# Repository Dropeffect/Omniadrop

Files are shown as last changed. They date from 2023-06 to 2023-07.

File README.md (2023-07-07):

# Dropeffect GitHub
Welcome to the Dropeffect GitHub repository. This is a place to share the instructions, models, adapters and any other relevant files for the Dropeffect products from Dropeffect R&D team and other users. 

Check the folders under the product name to find the file you need. We will continue updating the folders.

# How to buy Dropeffect products
Check the reseller list from Dropeffect website: www.dropeffect.com/pages/resellers

# Note
Thank you for using Dropeffect products. If you have any questions during use, please do not hesitate to contact us: contact@dropeffect.com. We will work with you to solve it. 

For more product information you can always follow Dropeffect Website/Twitter/Instagram/Facebook/Youtube and GitHub. Thank you!

Dropeffect Website: www.dropeffect.com

Dropeffect Twitter: www.twitter.com/dropeffect

Dropeffect Instagram: www.instagram.com/drop_effect

Dropeffect Facebook: www.facebook.com/Dropeffect

Dropeffect Youtube: www.youtube.com/@DropEffect

# Youtube link
Detailed introduction video: www.youtube.com/watch?v=j66pk6BJIjA

# Disclaimers
All models are shared for personal use only and commercial use is prohibited.

Models reuploaded base on original author's statement.

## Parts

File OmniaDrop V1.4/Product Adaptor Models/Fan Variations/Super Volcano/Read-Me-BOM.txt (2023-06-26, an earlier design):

You need the following additional materials:

1x 4010 Blower Fan
2x ISO4762 M2x4mm for the top holes of the 4010 blower fans
2x ISO4762 M2x6mm for the bottom holes of the 4010 blower fans
2x ISO7380 M3x8mm to attach the "Cooling-Two-Fan" to the "Cooling-Block-Fan"
4x M3 threaded inserts, these are there to attach a probe holder. The top two threaded insert are intended for a BLTouch probe holder and the the bottom two threaded inserts are intended for a induction probe holder.

For reference there are two pictures how to assemble everything.

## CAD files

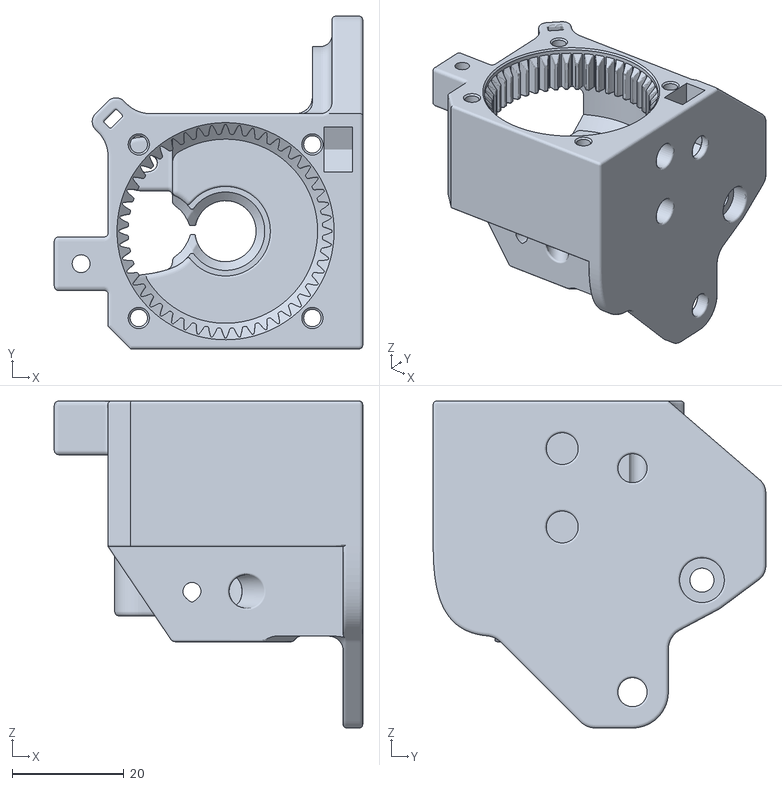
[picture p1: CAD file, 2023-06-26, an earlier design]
OmniaDrop V1.4/Product Adaptor Models/Ender 3/OmniaDrop-Elia-Ender3-Main 300 V1.4.stl
55.1 x 59.4 x 58.4

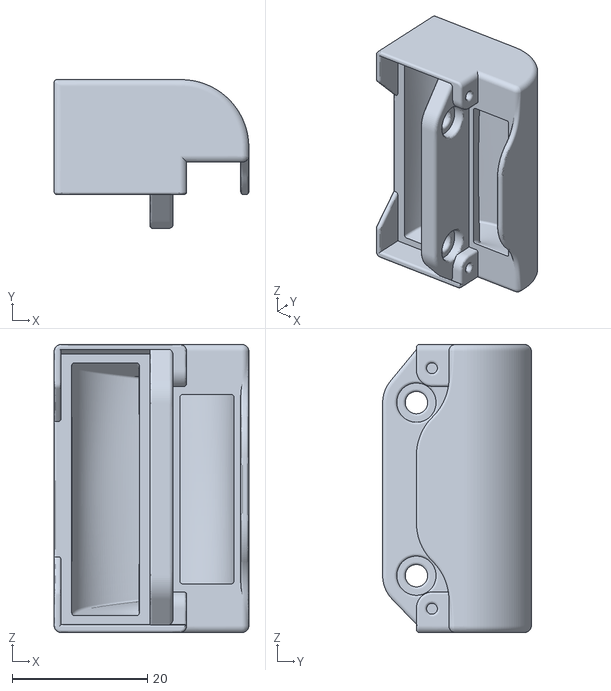
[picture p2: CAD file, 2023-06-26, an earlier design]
OmniaDrop V1.4/Product Adaptor Models/Fan Variations/Super Volcano/Cooling-Block-Fan-Super-Volcano.stl
28.8 x 22.0 x 42.6

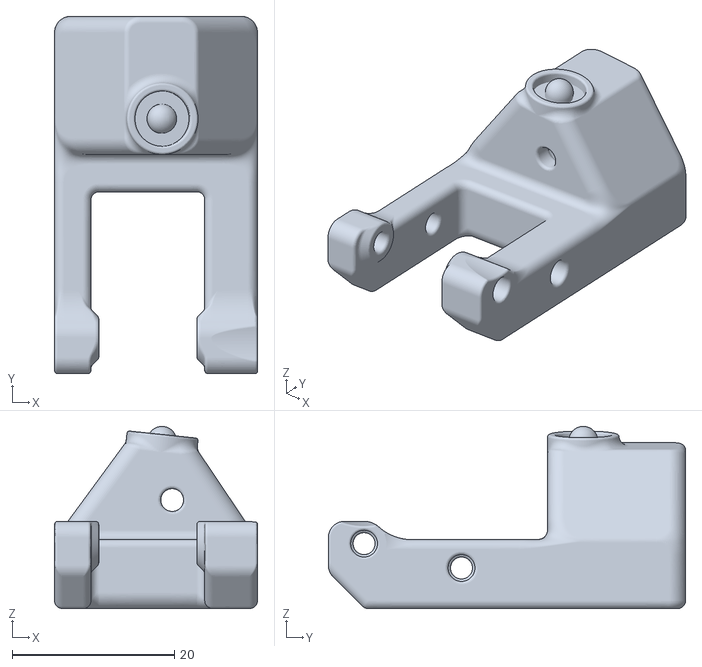
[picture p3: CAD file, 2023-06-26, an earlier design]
OmniaDrop V1.4/Product Adaptor Models/Idler Variations/OmniaDrop-175-Idler-Push-Fit.stl
25.0 x 44.0 x 22.4

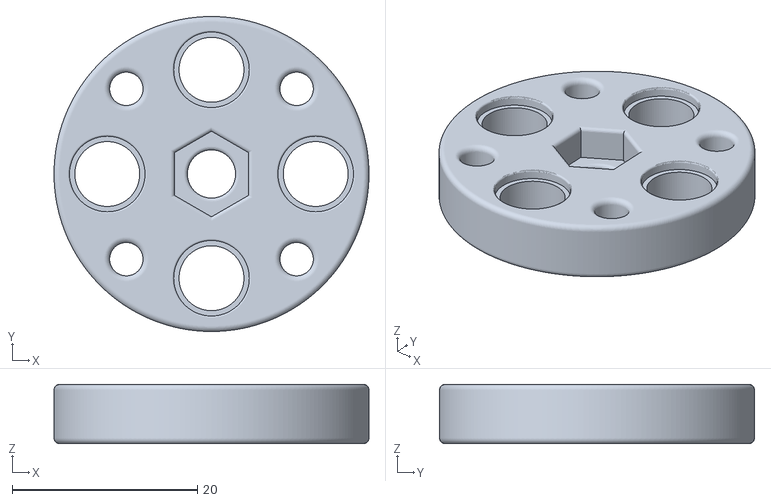
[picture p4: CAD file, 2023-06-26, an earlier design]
OmniaDrop V1.4/Product Adaptor Models/Planet-Disk V1.4.stl
34.0 x 34.0 x 6.40

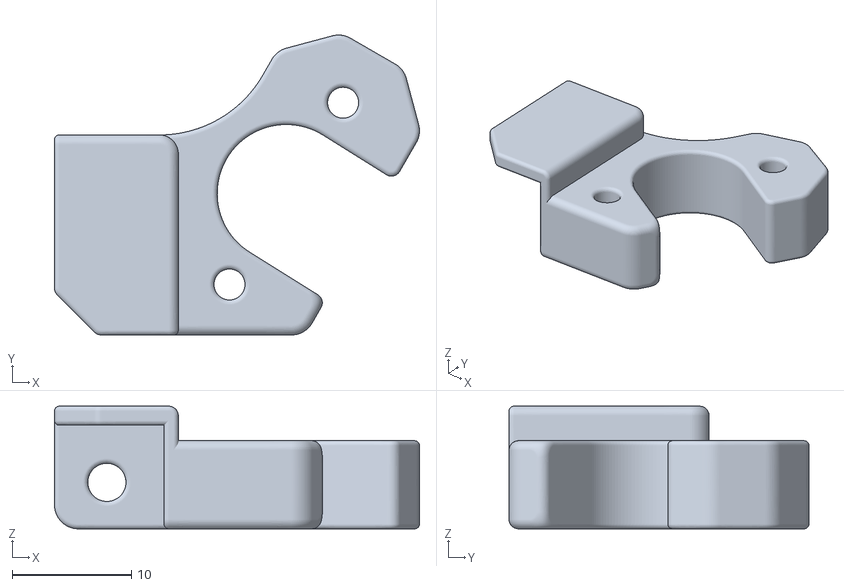
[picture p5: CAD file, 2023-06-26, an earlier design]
OmniaDrop V1.4/Product Adaptor Models/Probe Mounts/OmniaDrop-BLTouch-Clone.stl
30.7 x 25.2 x 10.3

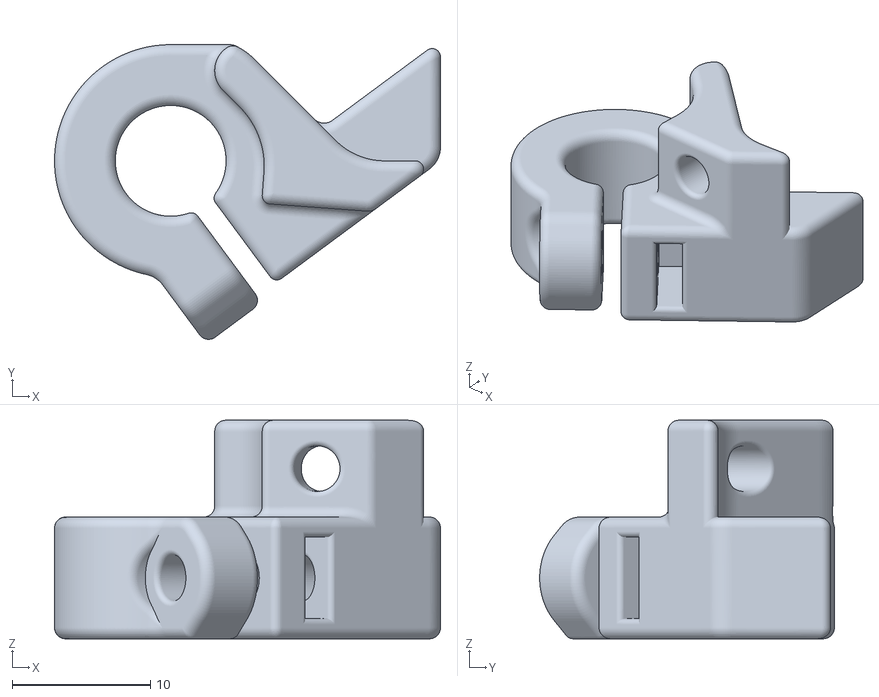
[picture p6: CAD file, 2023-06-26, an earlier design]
OmniaDrop V1.4/Product Adaptor Models/Prusa/OmniaDrop-Prusa-Probe 175 V1.4.stl
27.9 x 21.3 x 15.8

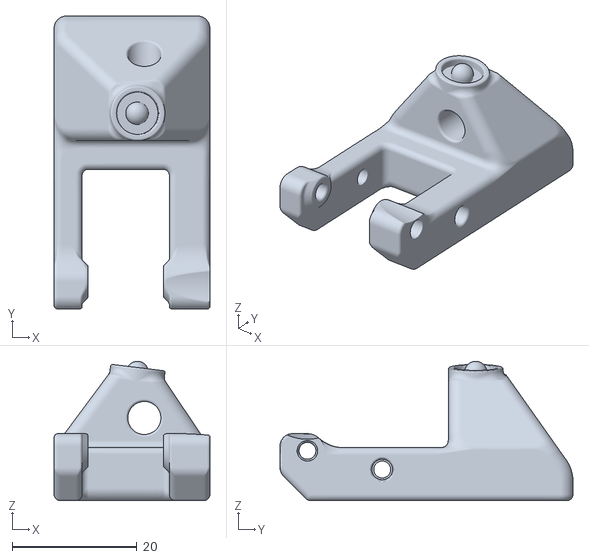
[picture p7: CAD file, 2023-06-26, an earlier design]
OmniaDrop V1.4/Product Adaptor Models/Standard/OmniaDrop-Idler 300 V1.4.stl
25.0 x 47.0 x 22.4

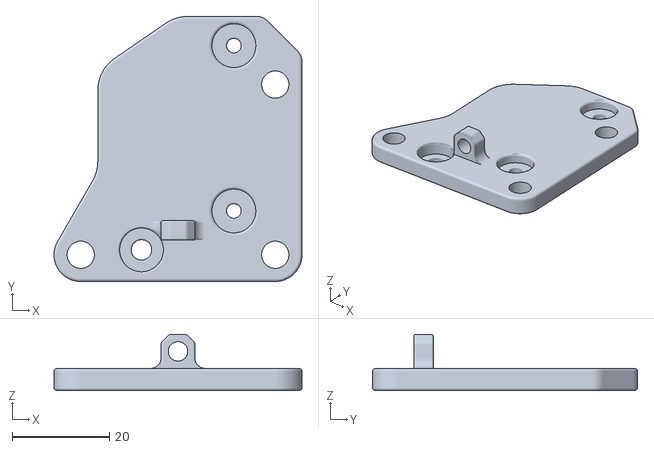
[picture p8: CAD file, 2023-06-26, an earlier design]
OmniaDrop V2.1/Product Adaptor Models/Artist-D Pro/OmniaDrop-Artist-D-Pro-Plate-right V2.1.stl
51.0 x 54.5 x 11.6

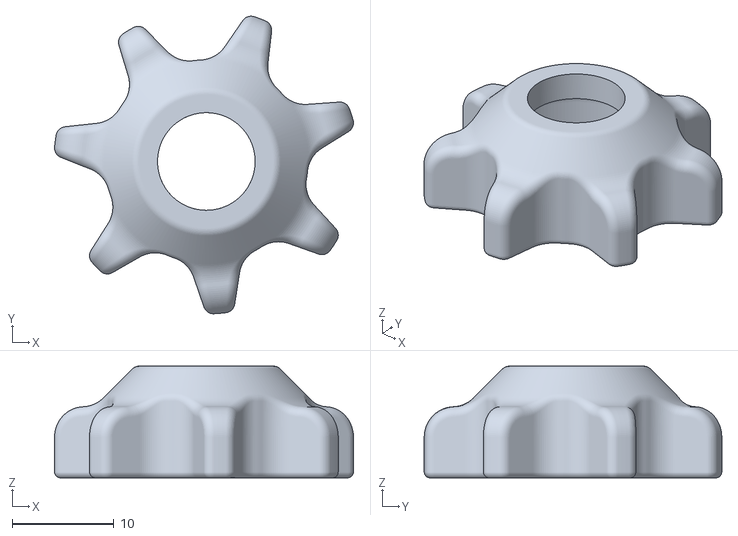
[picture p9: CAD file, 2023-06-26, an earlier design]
OmniaDrop V2.1/Product Adaptor Models/OmniaDrop-Manual-Wheel V2.stl
29.4 x 29.3 x 11.0

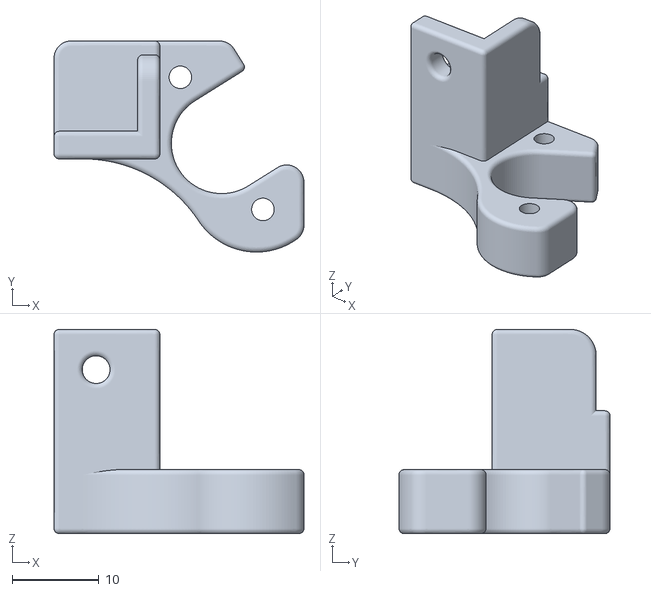
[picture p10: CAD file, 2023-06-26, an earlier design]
OmniaDrop V2.1/Product Adaptor Models/Probe Mounts/BLTouch-Clone-Mount.stl
28.9 x 24.4 x 23.6

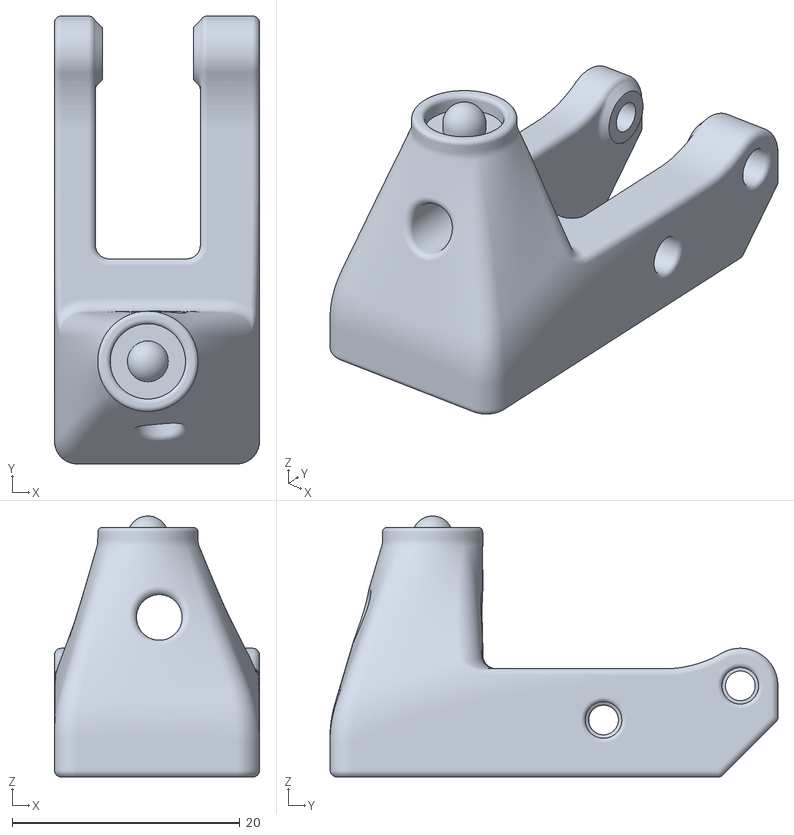
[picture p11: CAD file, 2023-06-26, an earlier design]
OmniaDrop V2.1/Product Adaptor Models/Prusa/OmniaDrop-Prusa-Idler V2.1.stl
18.0 x 39.3 x 22.9

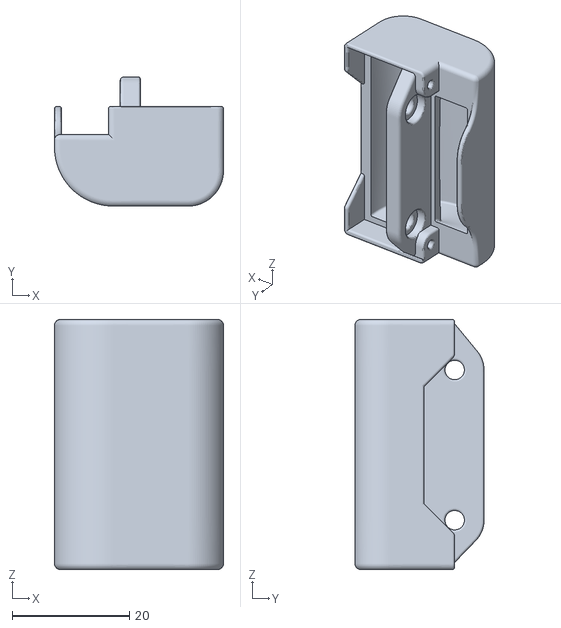
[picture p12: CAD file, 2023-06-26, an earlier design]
OmniaDrop V1.4/Product Adaptor Models/Only-Cooling-Block-Fan.stl
28.8 x 22.0 x 42.6

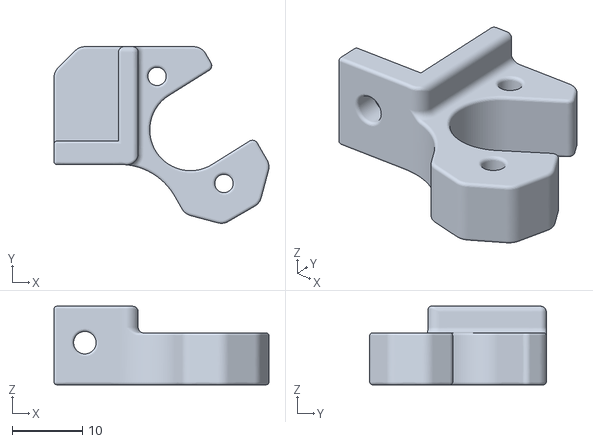
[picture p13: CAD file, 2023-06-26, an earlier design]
OmniaDrop V1.4/Product Adaptor Models/Probe Mounts/OmniaDrop-BLTouch-Standard.stl
30.7 x 25.2 x 11.2

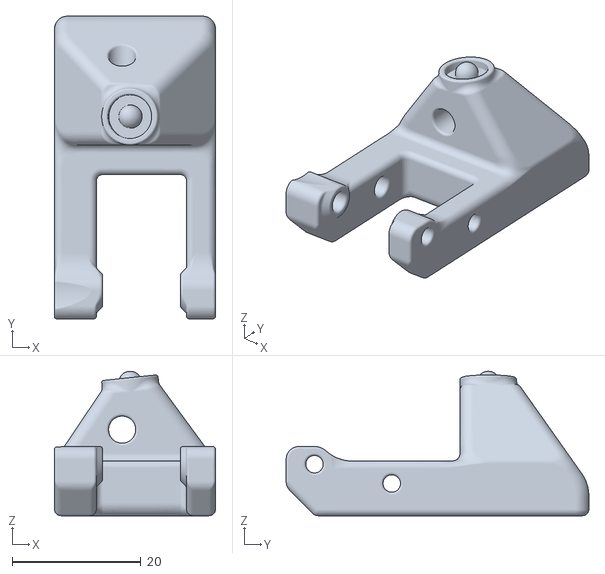
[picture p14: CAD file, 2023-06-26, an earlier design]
OmniaDrop V1.4/Product Adaptor Models/Prusa/OmniaDrop-Prusa-Idler 175 V1.4.stl
25.0 x 47.0 x 22.4

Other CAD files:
OmniaDrop V2.1/Product Adaptor Models/Standard/OmniaDrop-Idler-175 V2.1.stl
OmniaDrop V1.4/Product Adaptor Models/Standard/OmniaDrop-Manual-Wheel-ThreadedInsert.stl
OmniaDrop V2.1/Product Adaptor Models/Artist-D Pro/OmniaDrop-Artist-D-Pro-Plate-left V2.1.stl
OmniaDrop V2.1/Product Adaptor Models/Probe Mounts/BLTouch-Mount.stl
OmniaDrop V1.4/Product Adaptor Models/Probe Mounts/OmniaDrop-BLTouch-Volcano.stl
OmniaDrop V1.4/Product Adaptor Models/Probe Mounts/OmniaDrop-EZABL-18mm.stl
OmniaDrop V1.4/Product Adaptor Models/Standard/OmniaDrop-Idler 175 V1.4.stl
OmniaDrop V2.1/Product Adaptor Models/Prusa/OmniaDrop-Prusa-Cable V1.4.stl
OmniaDrop V2.1/Product Adaptor Models/Prusa/OmniaDrop-Prusa-Probe V2.1.stl

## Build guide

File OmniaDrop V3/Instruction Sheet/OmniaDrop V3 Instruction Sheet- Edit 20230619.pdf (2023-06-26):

## OmniaDrop Instructions and Assembly

## Dear customer, first of all thank you for purchasing the

## OmniaDrop V3 from DropEffect. When you open the

accessory package, you will find the following components.

No. | Name | Quantity
1 | H2.5 Hex Key | 1
2 | H2.0 Hex Key | 1
3 | H1.5 Hex Key | 1
4 | M5 Washer | 1
5 | Thermal Grease（0.5g） | 1
6 | M3 threaded inserts | 2
7 | M2 threaded inserts | 4
8 | H8.0 Open Spanner | 1
9 | Fan Extension Cable-5cm / JST-XHP | 2
10 | Motor Extension Cable-5cm / JST-XHP | 1
11 | Thermistor Extension Cable-5cm / JST-XHP | 1
12 | Heater Extension Cable-5cm | 1
13 | Fan Extension Cable-5cm / DuPont | 2
14 | Motor Extension Cable-5cm / DuPont | 1
15 | Thermistor Extension Cable-5cm / DuPont | 1

## Printing parameters

The nozzle size for printing the OmniaDrop parts should be a 0.4 mm nozzle or smaller. You should use 3 or more perimeters and 25% infill or more.

This part is important there should be no Z-Seam inside the blue sections of the OmniaDrop Extruder Main Body. The problem with a Z-Seam in these areas is that two ball bearings will be inserted into these grooves and if there is a Z-Seam in these areas then the planetary gears system will be off-centered and as such will not run smoothly. In your slicer it should be possible to edit your settings to position your Z-Seam accordingly.

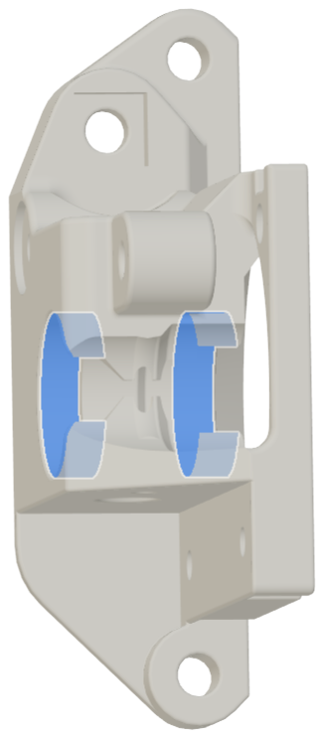
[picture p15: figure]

## Preparing the 3D printed parts

Components | QTY
Cooling fan duct | 1
Manual Wheel | 1
Extruder Main Body | 1
M2 threaded inserts | 4
M3 threaded inserts | 2
M6 threaded insert | 1

Use a soldering iron to insert the threaded inserts into the 3D printed parts. Ensure that the threaded inserts are flush and perpendicular. Be careful when using a soldering iron, they are very hot and you can burn yourself severely.

To get the M6 threaded insert of the manual wheel perpendicular you can use the Idler Dual Drive Gear (the shorter of the two Dual Drive Gear) as a base. Put the Idler Dual Drive Gear onto a non-flammable surface and put the manual wheel on top of it. This will ensure that the M6 threaded insert is inserted perpendicular and not too deep.

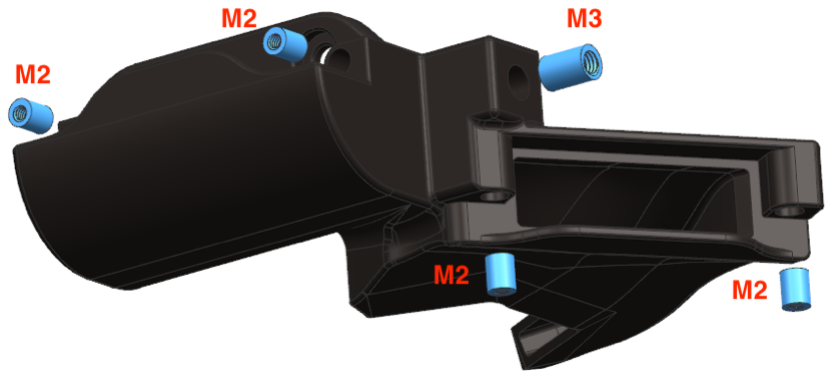
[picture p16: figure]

## Step 1

Components | QTY
M3x10 Hexagon button head screw | 4
Planetary gears | 4
Flanged ball bearings (F683 ZZ) | 8
Drive shaft (Planet Disk) | 1

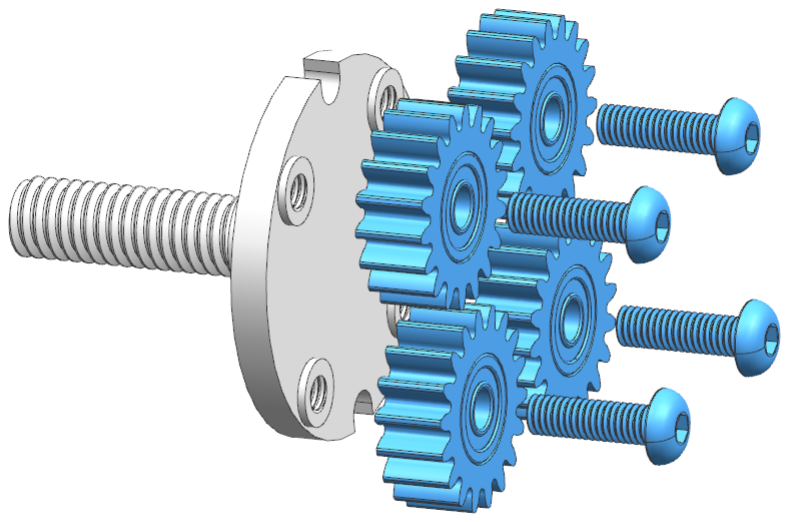
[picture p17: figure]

Insert two F683 ZZ ball bearings into a planet gear. Now use a M3×10 screw to attach the planet gear onto the Planet Disk. Please ensure that the planet gear is orientated in such a way that the protruding ball bearing of the planet gear interfaces with the Planet Disk. Repeat this for the remaining three planet gears.

## Step 2

Components | QTY
M6 threaded Drive Gear | 1
16 mm Ball Bearing (688ZZ W4) | 1
Extruder Main Body | 1

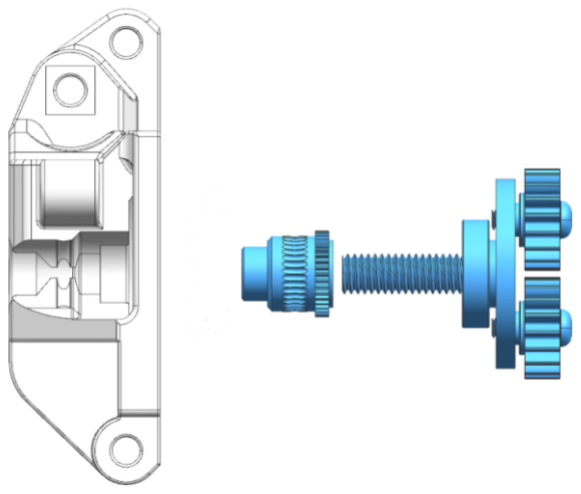
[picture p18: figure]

Put a 688ZZ W4 ball bearing (16 mm Diameter) onto the drive shaft of the Planet Disk. Tighten the M6 threaded drive gear onto the drive shaft. Finally insert the assembled drive shaft into the center hole of the extruder main body.

## Step 3

Components | QTY
M3 washer | 1
M3x8 Hexagon button head screw | 1
16 mm Ball Bearing (688ZZ W4) | 1
Manual Wheel | 1

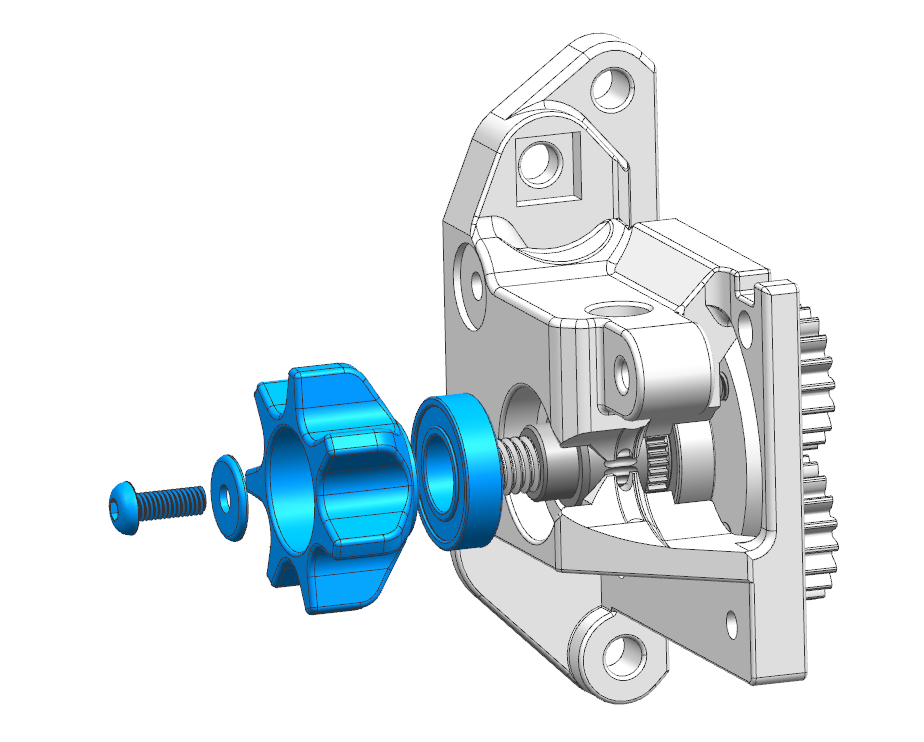
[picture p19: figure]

Press the 688ZZ W4 drive gear bearing into the front groove of the extruder main body. Then thread the manual wheel on the drive shaft to tighten everything down. Secure the position of the manual wheel by using a M3 washer and a M3x8 screw.

## Step 4

Components | QTY
M4x16 Hexagon button head screw | 1
Knurled nut | 1
M4 Square nut | 1
Spring | 1
Collect | 1
Collect clip | 1

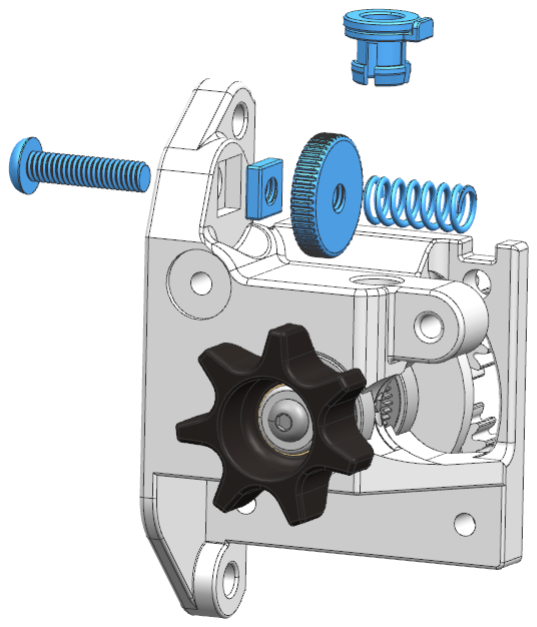
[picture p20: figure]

Insert the collect into the extruder main body and fix it with the collect clip. Insert the M4 square nut into the rectangular groove of the extruder main body and use the M4x16 screw to tighten everything down. Screw the knurled nut onto the M4 screw and place the compression spring onto the screw.

## Step 5

Components | QTY
M3x16 Hexagon button head screw | 2
Idler gear | 1
7mm ball bearing (683ZZ) | 2
Idler gear arm | 1

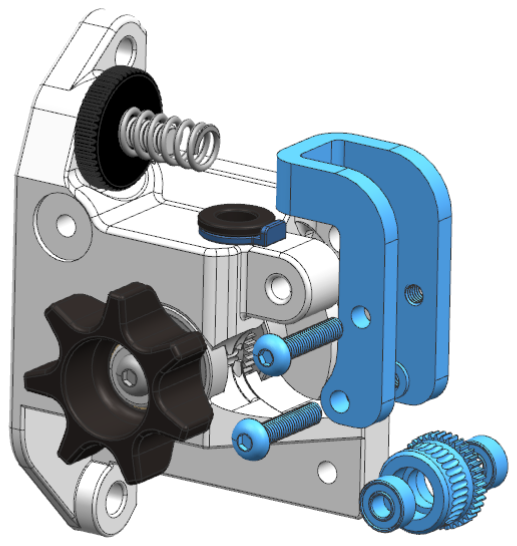
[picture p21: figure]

Insert two 683ZZ ball bearings into the internal holes of the idler gear. Place the Idler gear with the two ball bearings at bottom hole of the idler gear arm. Use a M3x16 screw to fix the position of the Idler gear; do not tighten it down too much, ensure that the Idler gear can spin freely. Use the second M3x16 screw to attach the Idler arm to the extruder main body. Again, do not tighten down the screw too much. The intention of these two M3x16 screws is not to tighten anything down, they should just hold the Idler gear and arm in position.

## Step 6

Components | QTY
M3x10 Hexagon button head screw | 1
M3x35 Hexagon button head screw | 1
M3 washer | 1
Ring Gear | 1
Nema 17 | 1

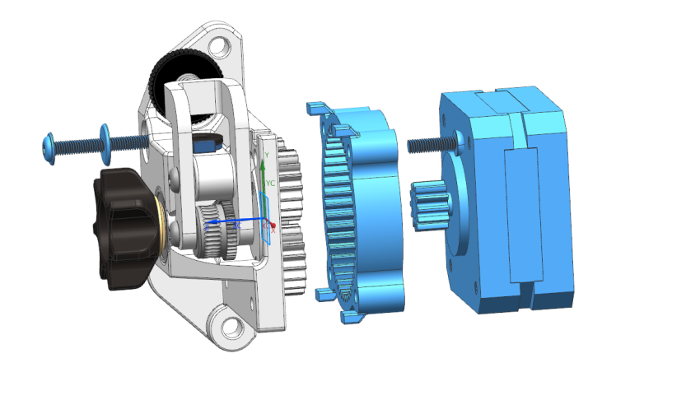
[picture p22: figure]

Attach the ring gear on the extruder main body. The four pegs on the ring gear should glide into the extruder main body. There are two indentations on the four 3 mm through holes of the ring gear, these should be orientated so that they are at the top section of the extruder main body. Use a M3×10 screw to secure the ring gear on the extruder main body. Now install the Nema 17 stepper motor on the planetary gear system and secure it using a M3x35 screw with a M3 washer.

## Step 7

Components | QTY
Heatbreak | 1
Thermal grease | 1
M3x35 Hexagon button head screw | 2
Heatsink | 1
Ring Heater | 1
Nozzle | 1

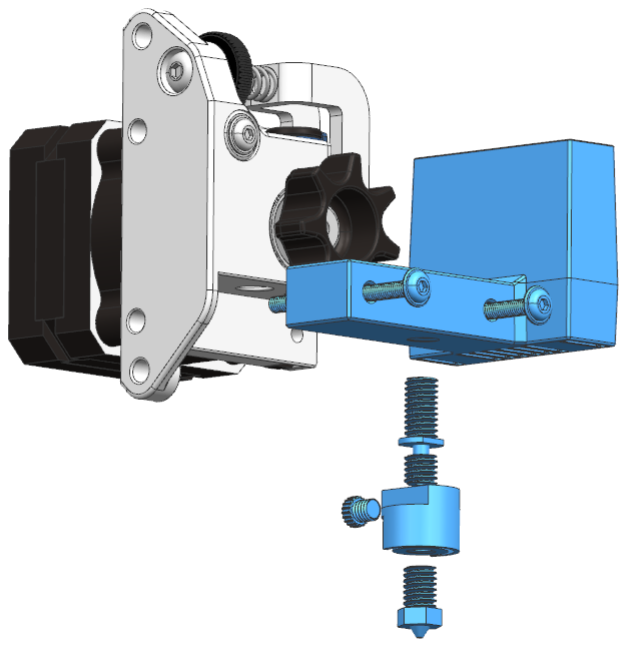
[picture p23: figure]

Apply some thermal grease onto the long threads of the heat break and screw it into the heat sink. Do NOT apply thermal grease onto the short threads of the heatbreak. Screw the Ring Heater with the indentations facing towards the heatsink onto the short thread of the heatbreak until no more threads are visible. However, do NOT screw the Ring Heater until it touches the heatsink, the “bottle neck” section of the heatbreak should always be visible. Orientate the cables of the Ring Heater so that they are facing the stepper motor. Finally, screw the nozzle into the Ring Heater and tighten it down. Please ensure that you do NOT put too much strain on the cables. Use some pliers or the 8mm open spanner to hold onto the Ring Heater while tightening the nozzle. If you followed the previous instructions correctly there should now be a gap (1-2 mm) between the nozzles and the Ring Heater (this is intentional). The gap between the nozzle and Ring Heater is a visual confirmation that you tightened the nozzle against heatbreak and not the Ring Heater. Now attach the heatsink to the extruder main body using the two M3x35 screws.

## Step 8

Components | QTY
M3x10 Hexagon button head screw | 1
M3 Washer | 1
M2x6 Hexagon cap head screw | 2
M2 Washer | 2
4010 Blower fan | 1
(Optional) BLTouch probe holder | 1

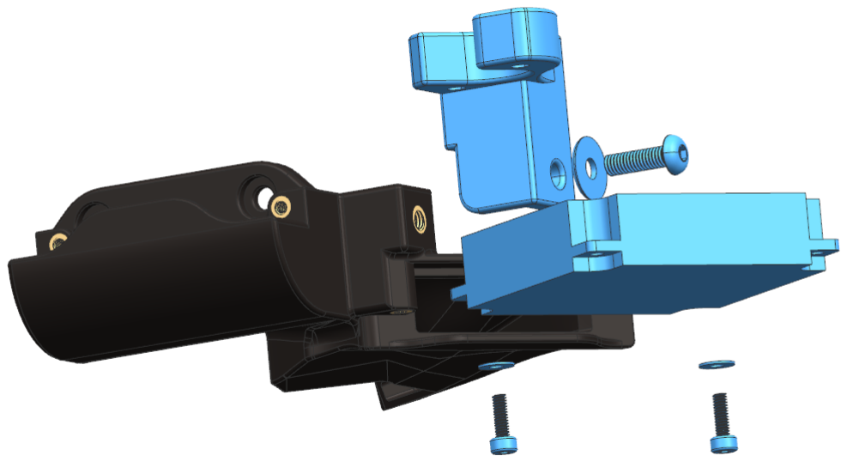
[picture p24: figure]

Use two M2x6 screws and two M2 washer to attach the 4010 blower fan to the part cooling fan duct.

Optionally you can attach the BLTouch probe holder to the probe holder peg on the cooling fan duct, however you can do this also later on.

## Step 9

Components | QTY
M3x10 Hexagon button head screw | 2
M2x6 Hexagon cap head screw | 2
M2 Washer | 2
4010 Blower fan | 1

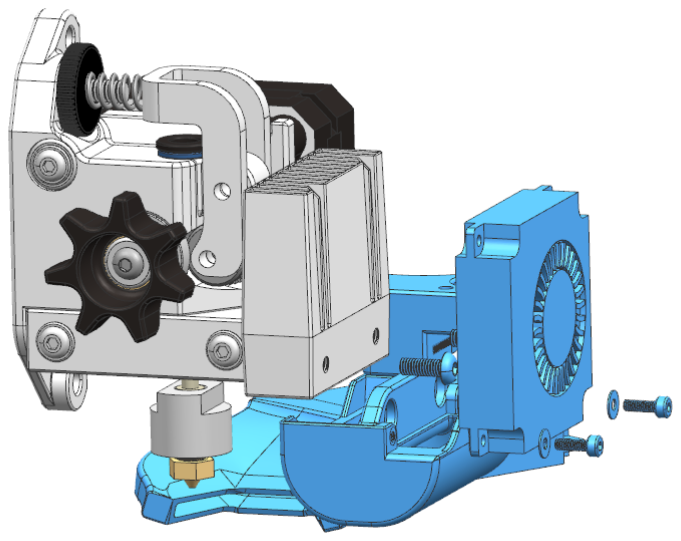
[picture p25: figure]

Clip the cooling fan duct to the bottom of the heat sink and secure it using two M3x10 screws. Then insert the 4010 blower fan into the cooling duct and tighten it with two M2x6 screws and M2 washers.

You are now all done, the OmniaDrop has now been assembled. After you have installed your OmniaDrop on your 3D printer please ensure you do the following steps:

- Adjust the current to extruder stepper motor to 600 mA (peak) (RMS = 425 mA)
- Adjust E-Steps to 480 steps/mm (x16 Microstepping)
- PID autotune the hotend
- Hot tighten the nozzle at 285°C

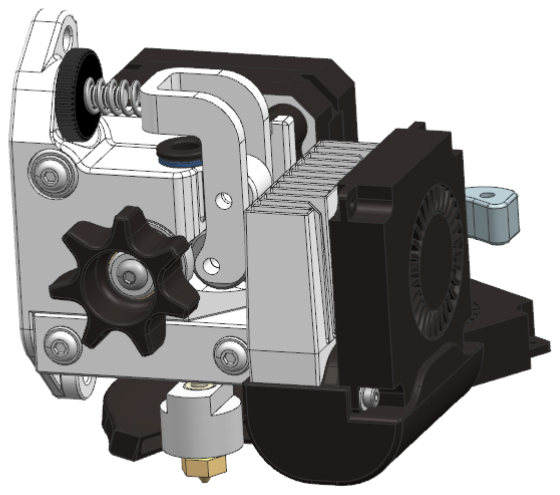
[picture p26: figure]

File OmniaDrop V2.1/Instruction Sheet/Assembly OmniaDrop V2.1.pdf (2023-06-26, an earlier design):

## Assembly OmniaDrop V2.1

Tools:
- Hex key 1.5 mm
- Hex key 2 mm
- 10 mm wrench (you can get away with pliers)
- 7 mm socket spanner or wrench

If you have the OmniaDrop Prusa edition follow the same instructions as the OmniaDrop Standard Edition, they do not differ, if not otherwise stated.

## Step 1

Items:

- Ring Heater
- 0.4 mm Nozzle

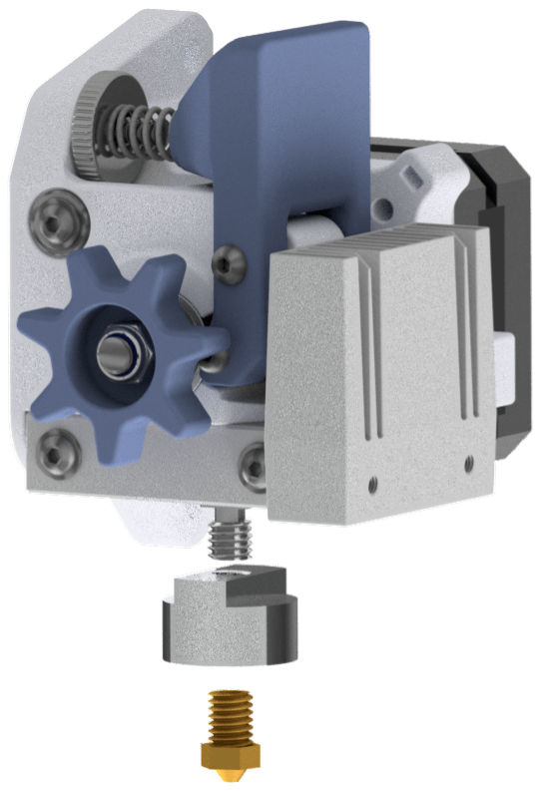
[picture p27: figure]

Screw the Ring Heater with the indentations facing towards the heatsink onto the heatbreak until no more threads are visible. However, do NOT screw the Ring Heater until it touches the heatsink, the “bottle neck” section of the heatbreak should always be visible. Orientate the cables of the Ring Heater so that they are facing the stepper motor. Finally, screw the nozzle into the Ring Heater and tighten it down. Please ensure that you do NOT put too much strain on the cables. Use some pliers or a 8mm open spanner to hold onto the Ring Heater while tightening the nozzle. There should now be a gap (1-2 mm) between the nozzles hex section and the Ring Heater (this is intentional). The gap ensures that you tightened nozzle against heatbreak and there is no gap between the nozzle and the heatbreak and as such creates a continuous filament path with no gaps.

Attach your OmniaDrop Standard Edition onto your 3D printer carriage.

## Step 2

Items:

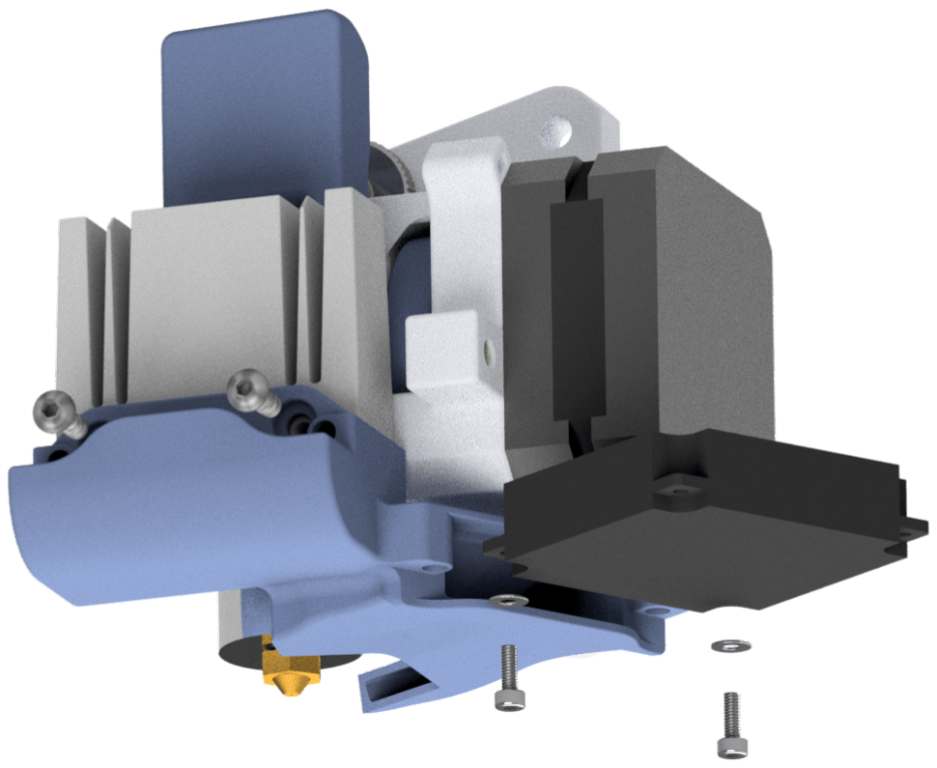
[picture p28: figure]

- 2 x M3x8
- 2 x M2x6
- 2 x M2 washer

Secure one of the blower fans with two M2x6 screws and M2 washers on the cooling duct. If you lose a M2 washer do not worry about it, it will work without it as well. For the Prusa edition the blower fan needs to be upside down.

With the two M3x8 screws attach the cooling duct to the cooling block.

## Step 3

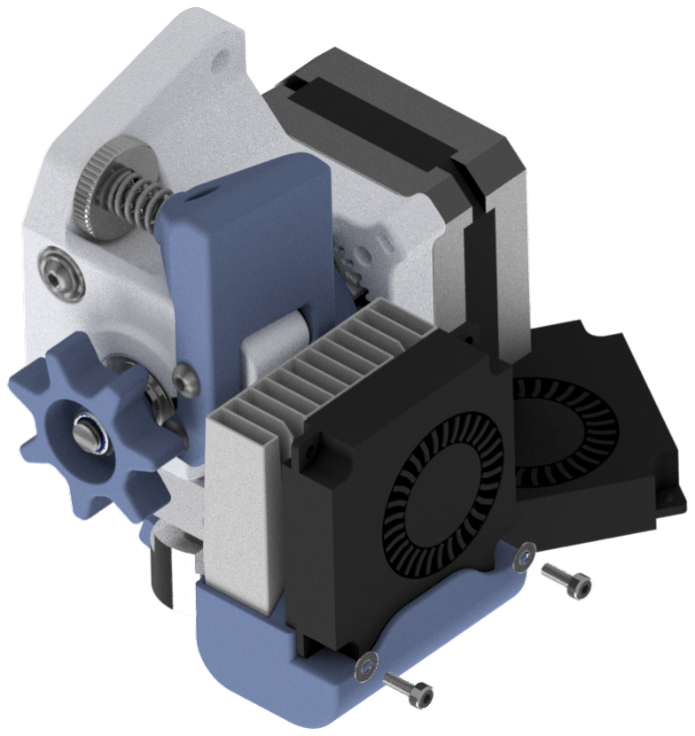
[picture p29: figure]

Items:

- 2 x M2x6
- 2 x M2 washer

Take the last blower fan and install it on the cooling duct. Use the two M2x6 screws and M2 washers to secure the blower fan. Again if you lose a M2 washer just install the fan without the M2 washers.

If you have the OmniaDrop Prusa Edition then go to the chapter “Prusa Edition” which guide you through the steps on how to install your OmniaDrop Prusa Edition.

## BLTouch (optional)

Items:

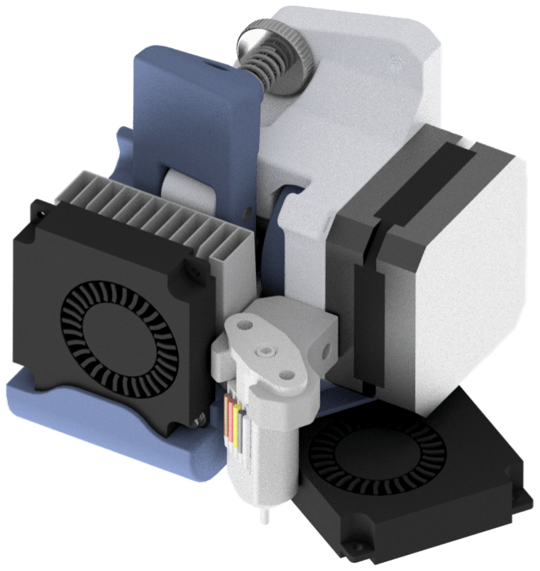
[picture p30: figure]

- 2 x M3x8
- 2 x M3 washer

Attach the BLTouch to the probe holder using the two M3 screws and the M3 washers. Then attach the probe holder on the small standoff of the OmniaDrop extruder.

The probe_offsets are X = 32.4 mm and Y = 34.9 mm. Depending on your printer and how the firmware is configured those offset can be negative. Usually the Y probe offset is negative so Y = -34.9 mm.

## Ender 3 Edition

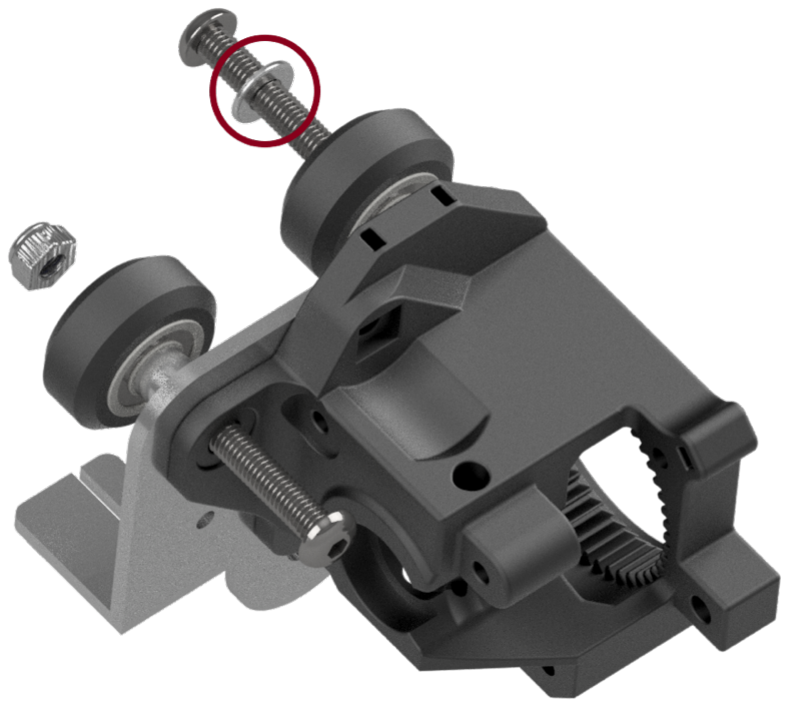
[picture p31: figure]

Items:

- 1 x M5 washer

Attach the OmniaDrop Ender 3 Edition to the Ender 3 X-carriage according to the picture.

Please do not forget to place the M5 washer on the M5x30 screw which fixes the V-slot wheel closest to the stepper motor.

## LAST STEPS

Adjust Current

First you should adjust the current to the extruder stepper motor. The stepper motors require the following currents:
- small stepper motor (body length 20 mm) set current to 0.6A
- bigger stepper motor (body length 34 mm) set current to 0.85A.

Depending on your stepper driver and electronic controller you need to either adjust the current in the firmware or manually using a trim pot on the stepper driver.
If you have a A4988 driver set a 0.5 Vref for the small stepper motor and a 0.7 Vref for the bigger stepper motor. If the motor gets too hot then decrease the current. As a rule of thumb after 20-30 minutes of printing you should be able to hold your fingers for 5 seconds on the stepper motor.

Update steps/mm value

To adjust your steps/mm value use the M92 G-code and then save that new value to EEPROM using the Gcode M500. Your G-code file should look like this:

M92 E[steps/mm]
M500

For the 1.75 mm Filament OmniaDrop version the steps/mm value is 480 steps/mm for 1/16 microstepping. The G-code should look like this: M92 E480

For the 3 mm Filament OmniaDrop version the steps/mm value is 560 steps/mm for 1/16 microstepping. The G-code should look like this: M92 E560

Hot tightening

Next you need to heat up the hotend to 285°C. Once the hotend reached the temperature hold the hotend in place using pliers or a 10 mm wrench and tighten the nozzle using a 7 mm socket spanner or wrench. Be careful not to use too much force otherwise you will damage the Heatbreak or the nozzle.

To make sure that the temperature is stable during printing do a PID autotune/calibration.

Thermistor

The thermistor is a NTC 100K 1% 4267. In Marlin firmware that would be thermistor number "5".

### PRUSA EDITION

Remove the old extruder from your Prusa. Attach the OmniaDrop extruder to your Prusa using zip ties and insert the GT2 belt into the intended slots.

Prusa Cable Management

Items from Bag 1:

- 1 x M3x50
- 2 x M3 square nut
- 2 x M3x14

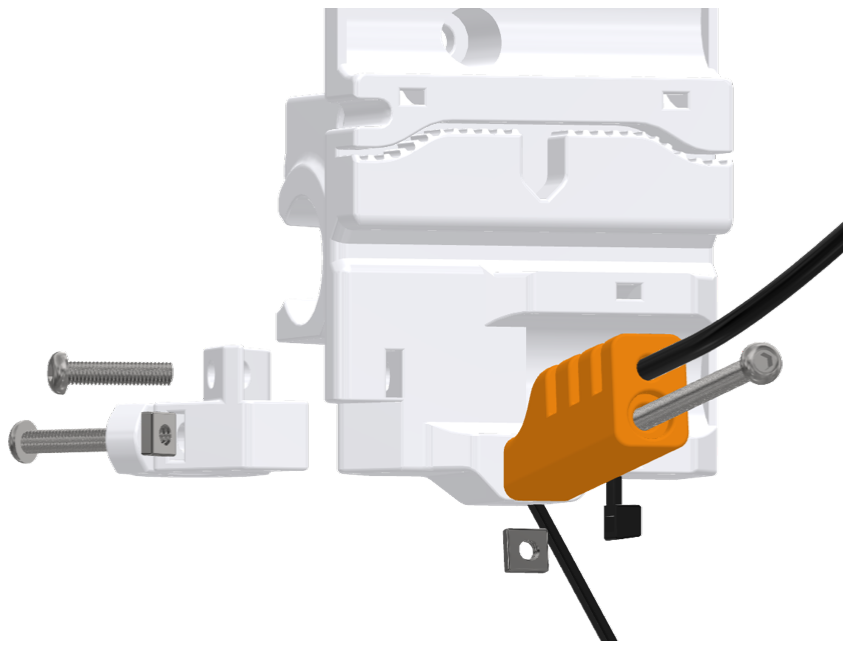
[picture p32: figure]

Wire all the cables (except the PINDA probe cable) at the bottom of the OmniaDrop-Main body and secure the cable to OmniaDrop-Main body using a zip tie, like shown in the image.

Attach the cable holder to the OmniaDrop-Main body using a M3 square nut and the M3x50 screw. Make sure to orientate the cable holder like shown in the image.

Attach the PINDA probe to the OmniaDropprobe-holder using the M3x14 screw and M3 square nut and mount it to the OmniaDrop-Main body using another M3x14 screw.. Wire the PINDA probe cable above the GT2 belt and then down to the cable holder.

Insert the Nylon cable guide in the cable holder and attach all the cables to the cable holder using three zip ties.

Original Prusa MK3

To adjust your steps/mm value use the M92 G-code and then save that new value to EEPROM using the Gcode M500. Your G-code file should look like this:

M92 E960
M500

Next you need to heat up the hotend to 285°C. Once the hotend reached the temperature hold the hotend in place using pliers or a 10 mm wrench and tighten the nozzle using a 7 mm socket spanner or wrench. Be careful not to use too much force otherwise you will damage the Heatbreak or the nozzle.

To do a PID calibration on a original Prusa MK3 go the LCD Menu

Calibration > PID calibration

Under Settings disable the following two features:

Filament sensor [off]
Fans check [off]

Adjust the PINDA probe to the correct height using the method mentioned in the Prusa assembly manual.

In your slicer you need to add the following line to your Start G-Code, after the G80 mesh bed leveling Gcode:

G1 X2.5 Y17.5 F3600
G92 X0 Y0

Remember the OmniaDrop Prusa Edition loses 17.5 mm at the back of the printbed.
Place your 3D model in your slicer in such a way that 3D model does not fall into these regions.

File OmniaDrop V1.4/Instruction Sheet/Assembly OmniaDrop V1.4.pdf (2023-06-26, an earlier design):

## Assembly OmniaDrop V1.4

Tools:
- Hex Key 1.5 mm
- Hex key 2 mm
- Hex key 2.5 mm
- 10 mm wrench (you can get away with pliers)
- 8 mm socket spanner (you can get away with pliers)
- 7 mm socket spanner or wrench
- 6 mm wrench

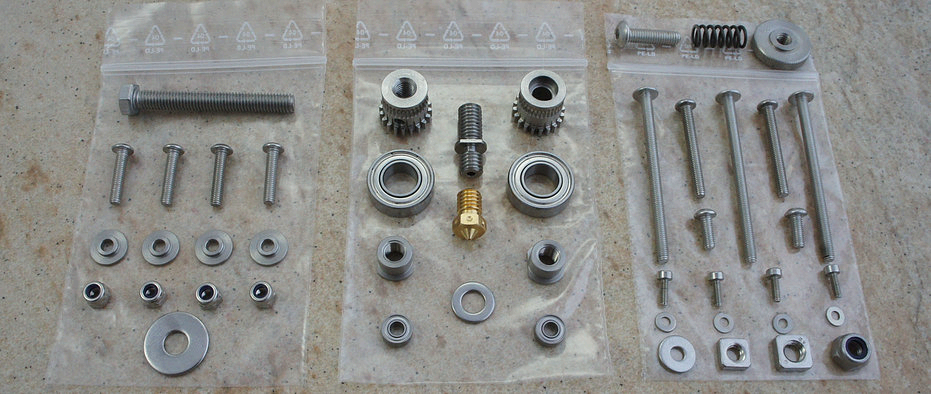
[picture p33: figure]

Bag 1 | Bag 2 | Bag 3

If you have the OmniaDrop Prusa edition follow the same instructions as the OmniaDrop standard version, they do not differ, if not otherwise stated.

If you have the OmniaDrop Pre-assembled version start at Step 9 (install the hotend and the nozzle) and then go to Step 11

## Step 1

Items from Bag 1:

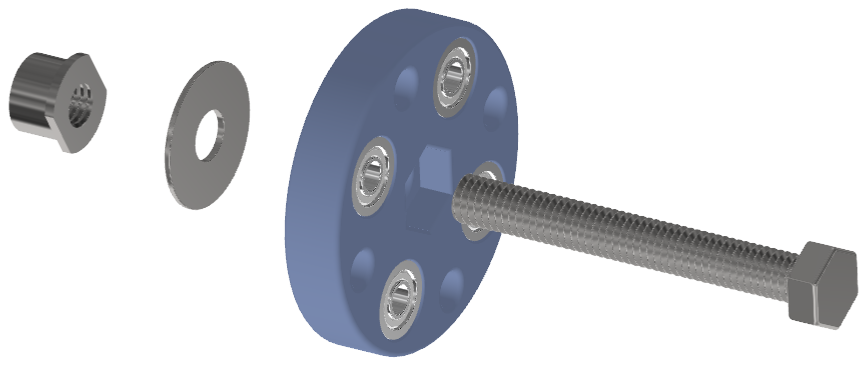
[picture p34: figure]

- 1 x M5x40
- 1 x M5 washer

Items from Bag 2:

- 1 x M5 Sleeve

Take the M5x40 screw and thread it through the Planet-Disk, orientated as shown in the image. Then place the M5 washer on the M5 screw and screw the M5 Sleeve onto the M5 screw. Tighten down the M5 Sleeve with a 8 mm wrench or pliers.

## Step 2

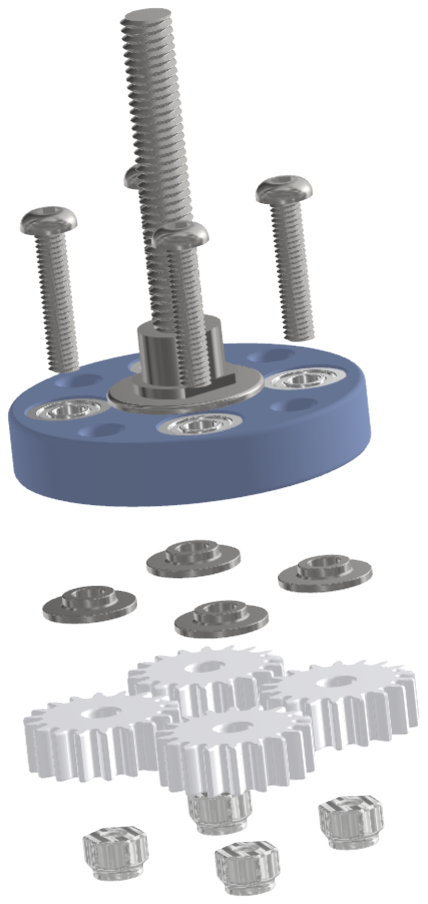
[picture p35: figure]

Items from Bag 1:

- 4 x M3x14
- 4 x M3 spacer
- 4 x M3 lock nut

Thread one of the M3x14 screws through the ball bearings of the Planet-Disk; make sure that the screw head is on
that side where the M5 Sleeve is. Place one M3 spacer with the small ring towards the ball bearings, on the screw. Insert a M3 lock nut with the blue ring facing upwards in the Planet-Gear. Screw that Planet-Gear on the M3 screw. The M3 screw should protrude 0.5-1mm the M3 lock nut. The Gears should not wobble or have play.
Repeat this procedure for the remaining three Planet-Gears.

## Step 3

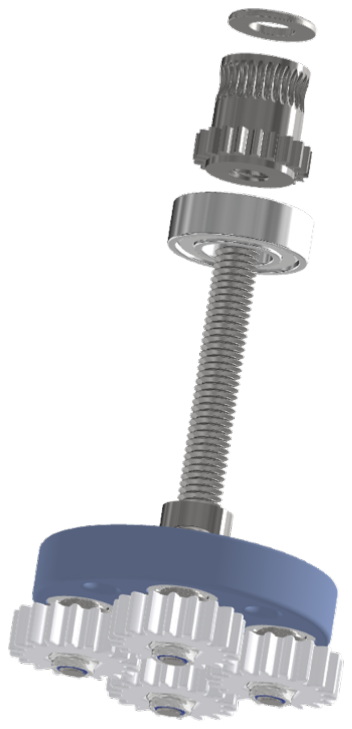
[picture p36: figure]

Items from Bag 2:

- 1 x 688 ZZ ball bearing
- 1 x Threaded Hobbed Gear
- 1 x M5 washer

Place the ball bearing on the M5 Sleeve and screw the Threaded Hobbed Gear onto the M5 screw orientated like in the image. Tighten the grub screw on the Hobbed Gear, to secure the Hobbed Gear. Now place the M5 washer on the M5 screw.

## Step 4

Items from Bag 2:

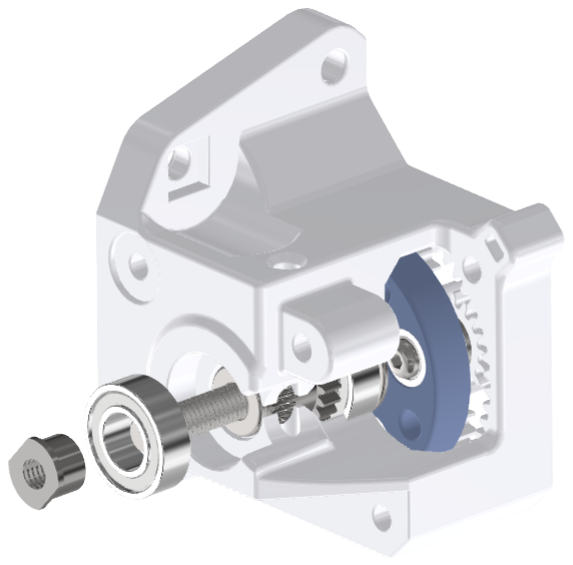
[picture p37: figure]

- 1 x 688 ZZ ball bearing
- 1 x M5 Sleeve

Insert the 688 ZZ bearing into the OmniaDrop-Main body. Install the Planetary Gear system in
the OmniaDrop-Main body in such a way that the teeth of the Hobbed Gear align with the filament path. Use a screwdriver to lock the Planetary Gear from turning and screw the M5 Sleeve on the M5 bolt to secure the Planetary Gear shaft. Tighten the M5 Sleeve with a wrench.

## Step 5

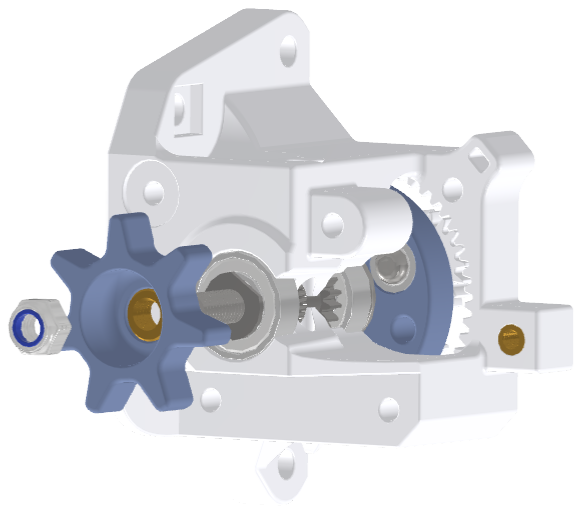
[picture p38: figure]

Items from Bag 3:

1 x M5 lock nut

Insert a long M3 screw into the 3 mm holes of the Planet Disk to lock the Planetary Gear and stop it from turning. Screw the Manual-Wheel onto the Planetary Gear shaft. Using the 8 mm socket spanner secure/tighten everything with the M5 lock nut. The Planetary Gear shaft should protrude 1-2 mm the M5 lock nut.

Make sure that the Manual-Wheel has no play. Remove the screw driver from locking the Planetary Gear and turn the Planetary Gear using the Manual Wheel. Check that the Planetary Gear can move.

## Step 6

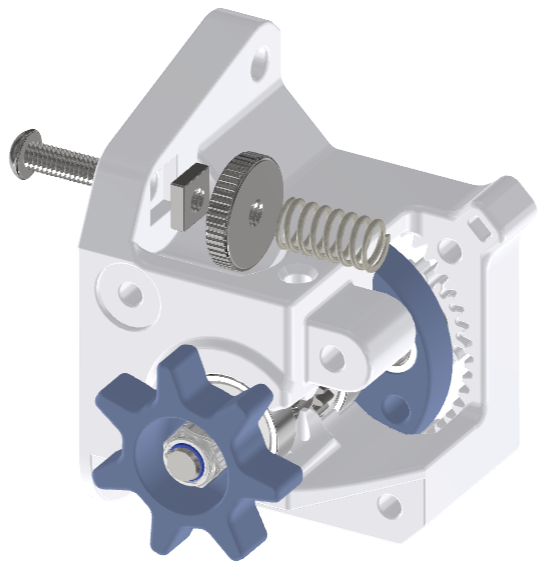
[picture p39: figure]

Items from Bag 3:

- 1 x M4x16
- 1 x M4 square nut
- 1 x M4 knurled nut
- 1 x Spring

Insert the M4 square nut into the OmniaDrop-Main body and screw the M4x16 from the back into the OmniaDrop-Main like shown in the image Then screw the knurled nut onto the M4 screw. Now place the spring on the M4 screw.

## Step 7

Items from Bag 2:

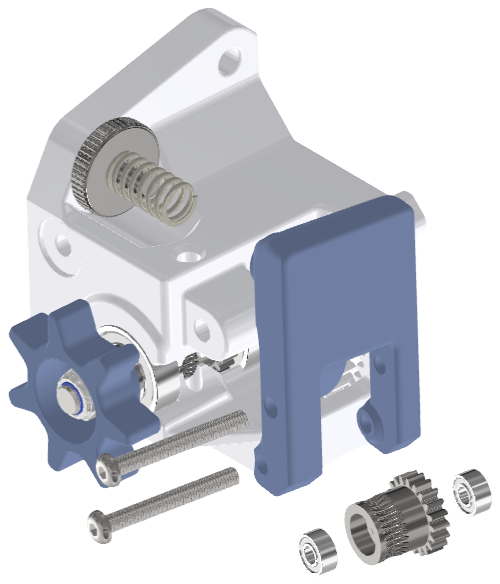
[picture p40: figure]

- 2 x 683 ZZ ball bearing
- 1 x Hobbed Gear Idler

Items from Bag 3:

- 2 x M3x25

Insert one 683 ZZ ball bearing on each side of the Hobbed Gear. Place the Hobbed Gear in between the two legs of the Idler and screw into place using the M3x25 screw. Do not overtighten the M3x25 screw, the Hobbed Gear Idler should rotate freely. Ensure that the orientation of the Hobbed Gear corresponds to the orientation in the image. Use the remaining M3x25 screw secure the Idler on the OmniaDrop-Main body. Do not over-tighten the M3 screw. The Idler should now have a 6° angle (tilt) to the OmniaDrop-Main body. This ensures the maximum possible grip for the filament and is intentional.

## Step 8

Items from Bag 3:

- 1 x M3x45
- 1 x M3 washer

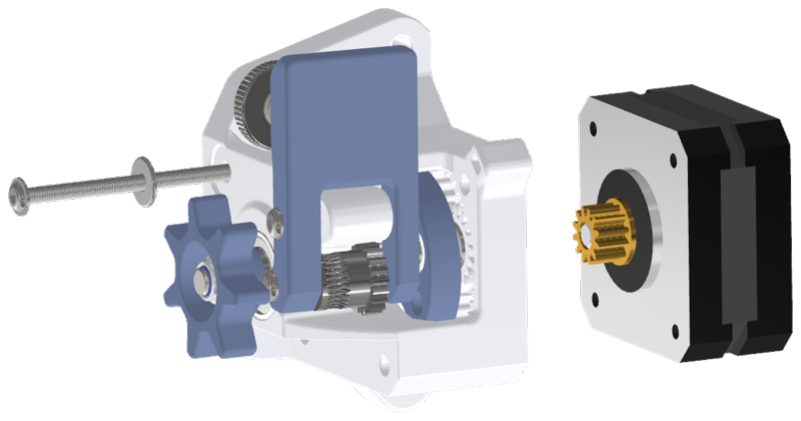
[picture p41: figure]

Take the stepper motor and jiggle it into the Planetary Gear system. Use the M3x45 screw and M3 washer to secure the stepper motor.

Due to the zero tolerance fit the Planetary-Gear will be very difficult or nearly impossible to rotate. Do NOT try to turn the Planetary-Gear manually. Once assembled you will have to run a G-code to run-in the Planetary-Gear. This G-code can be downloaded at the end of this assembly page.

## Step 9

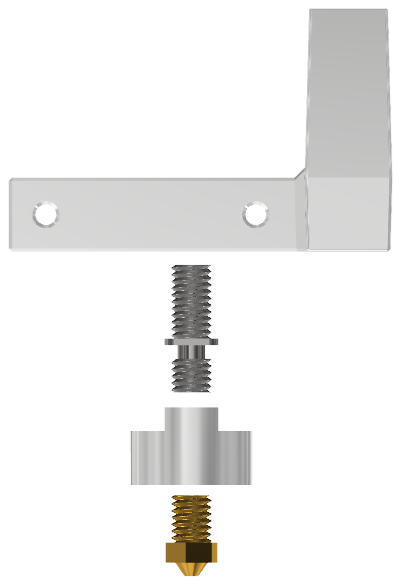
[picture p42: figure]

Items from Bag 2:

- Heatbreak
- 0.4 mm Nozzle

Screw the Nozzle all the way into to ring heater and then unscrew it one turn, so that there is a gap between the ring heater and the nozzle. Make sure the nozzle is screwed into the correct side of the ring heater like in the picture. Do not put too much strain on the cables of the ring heater.

## Step 10

Items from Bag 3:

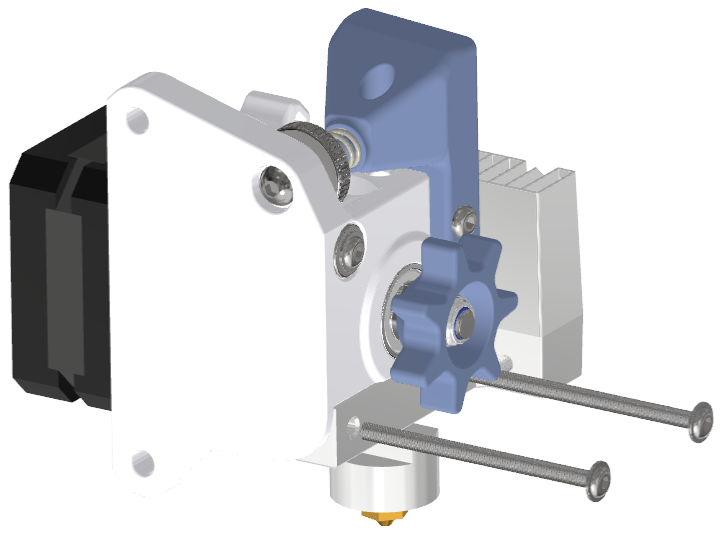
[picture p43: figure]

- 2 x M3x45

Use the two M3x45 screws to mount the cooling block onto the OmniaDrop-Main body. Make sure that the cables of the hotend are facing towards the stepper motor. If the Cables face the wrong way unscrew the nozzle slightly and orientate the cables correcly, then screw the nozzle back into the hotend.

Secure now the OmniaDrop standard version on your 3D printer carriage.

## Step 11

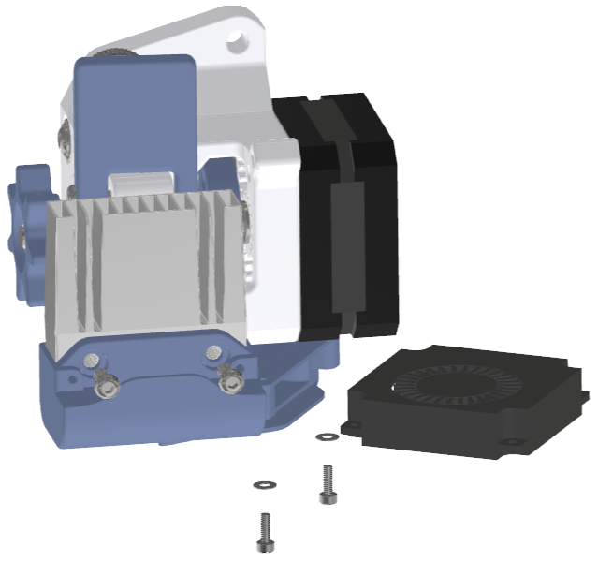
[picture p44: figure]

Items from Bag 3:

- 2 x M3x8
- 2 x M2x6
- 2 x M2 washer

Secure one of the blower fans with two M2x6 screws and M2 washers on the cooling duct. If you lose a M2 washer do not worry about it, it will work without it aswell. For the Prusa edition the blower fan needs to be upside down.

With the two M3x8 screws attach the cooling duct to the cooling block.

## Step 12

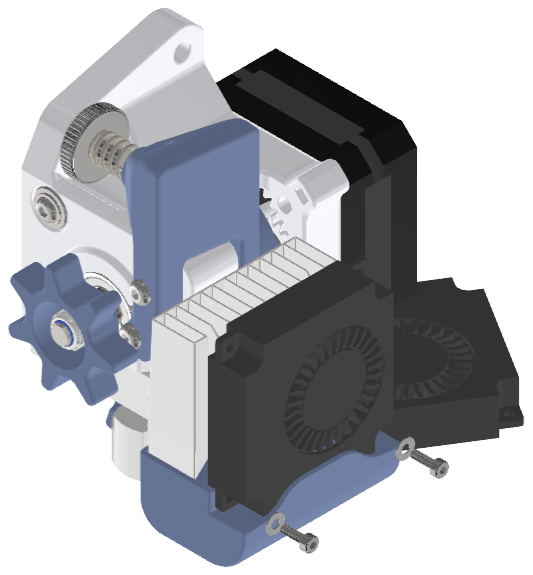
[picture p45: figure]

Items from Bag 3:

- 2 x M2x6
- 2 x M2 washer

Take the last blower fan and install it on the cooling duct. Use the two M2x6 screws and M2 washers to secure the blower fan. Again if you lose a M2 washer just install the fan without the M2 washers.

## LAST STEPS

Adjust Current

First you should adjust the current to the extruder stepper motor. The stepper motors have the following rated currents:

- small stepper motor (body length 20 mm) has a rated current of 1A.
- bigger stepper motor (body length 34 mm) for the 3 mm filament version has a rated current of 1.33A.

Depending on your stepper driver and electronic controller you need to either adjust the current in the firmware or manually using a trim pot. Generally speaking you should set the current to 65% of the rated current. If you have a A4988 driver set 0.5 Vref for the small stepper motor and 0.64 Vref for the bigger stepper motor. If the motor gets too hot then decrease the current. As a rule of thumb after 20-30 minutes of printing you should be able to hold your fingers for 10 seconds on the stepper motor.

Planetary-Gear break-in procedure

Create a Gcode file in a Text-editor like Notepad++ and write a Gcode that lets the Extruder rotate for 2-12 hours. Write the Gcode in such a way that the rotation is alternating every 10 minutes, meaning that the Manual Wheel rotates 10 minutes clockwise and then 10 minutes counterclockwise.

There should be NO FILAMENT LOADED when running this G-code. Make sure there is no filament loaded and run the G-code file on your printer. If the extruder starts skips steps and does not turn, aid the extruder by turning the manual wheel.

Update steps/mm value

Create a G-code file with a Text-editor like Notepad++ and use the M92 G-code command to update the steps/mm value for your OmniaDrop Version:

For the 1.75 mm Filament OmniaDrop version the steps/mm value is 480 steps/mm for 1/16 microstepping. In this case the fourth code line should look like this: M92 E480

For the 3 mm Filament OmniaDrop version the steps/mm value is 560 steps/mm for 1/16 microstepping. In this case the fourth code line should look like this: M92 E560

Hot tightening

After running the G-code file you should be able to manually turn the Planetary-Gear. Next you need to heat up the hotend to 285°C. Once the hotend reached the temperature hold the hotend in place using pliers or a 10 mm wrench and tighten the nozzle using a 7 mm socket spanner or wrench. Be careful not to use too much force otherwise you will damage the Heatbreak.

To make sure that the temperature is stable during printing do a PID autotune/calibration.

If you have the BLTouch you need to set your probe_offset to X = 32.4 mm and Y = 34.9 mm.

### PRUSA EDITION

Remove the old extruder from your Prusa. Attach the OmniaDrop extruder to your Prusa using zip ties and insert the GT2 belt into the intended slots.

Prusa Cable Management

Items from Bag 1:

- 1 x M3x50
- 2 x M3 square nut
- 2 x M3x14


Wire all the cables (except the PINDA probe cable) at the bottom of the OmniaDrop-Main body and secure the cable to OmniaDrop-Main body using a zip tie, like shown in the image.

Attach the cable holder to the OmniaDrop-Main body using a M3 square nut and the M3x50 screw. Make sure to orientate the cable holder like shown in the image.

Attach the PINDA probe to the OmniaDropprobe-holder using the M3x14 screw and M3 square nut and mount it to the OmniaDrop-Main body using another M3x14 screw.. Wire the PINDA probe cable above the GT2 belt and then down to the cable holder.

Insert the Nylon cable guide in the cable holder and attach all the cables to the cable holder using three zip ties.

Original Prusa MK3

To do a PID calibration on a original Prusa MK3 go the LCD Menu

Calibration > PID calibration

Under Settings disable the following two features:

Filament sensor [off]
Fans check [off]

Adjust the PINDA probe to the correct height using the method mentioned in the Prusa assembly manual.

In your slicer you need to add the following line to your Start G-Code, after the G80 mesh bed leveling G-Code:

G1 X0 Y17.5 F3600
G92 X7.5 Y0

Remember that the 7.5 mm on the left side of the printbed cannot be printed on and at the back 17.5 mm cannot be used. So place your 3D model in your slicer in such a way that 3D model does not fall into these regions.

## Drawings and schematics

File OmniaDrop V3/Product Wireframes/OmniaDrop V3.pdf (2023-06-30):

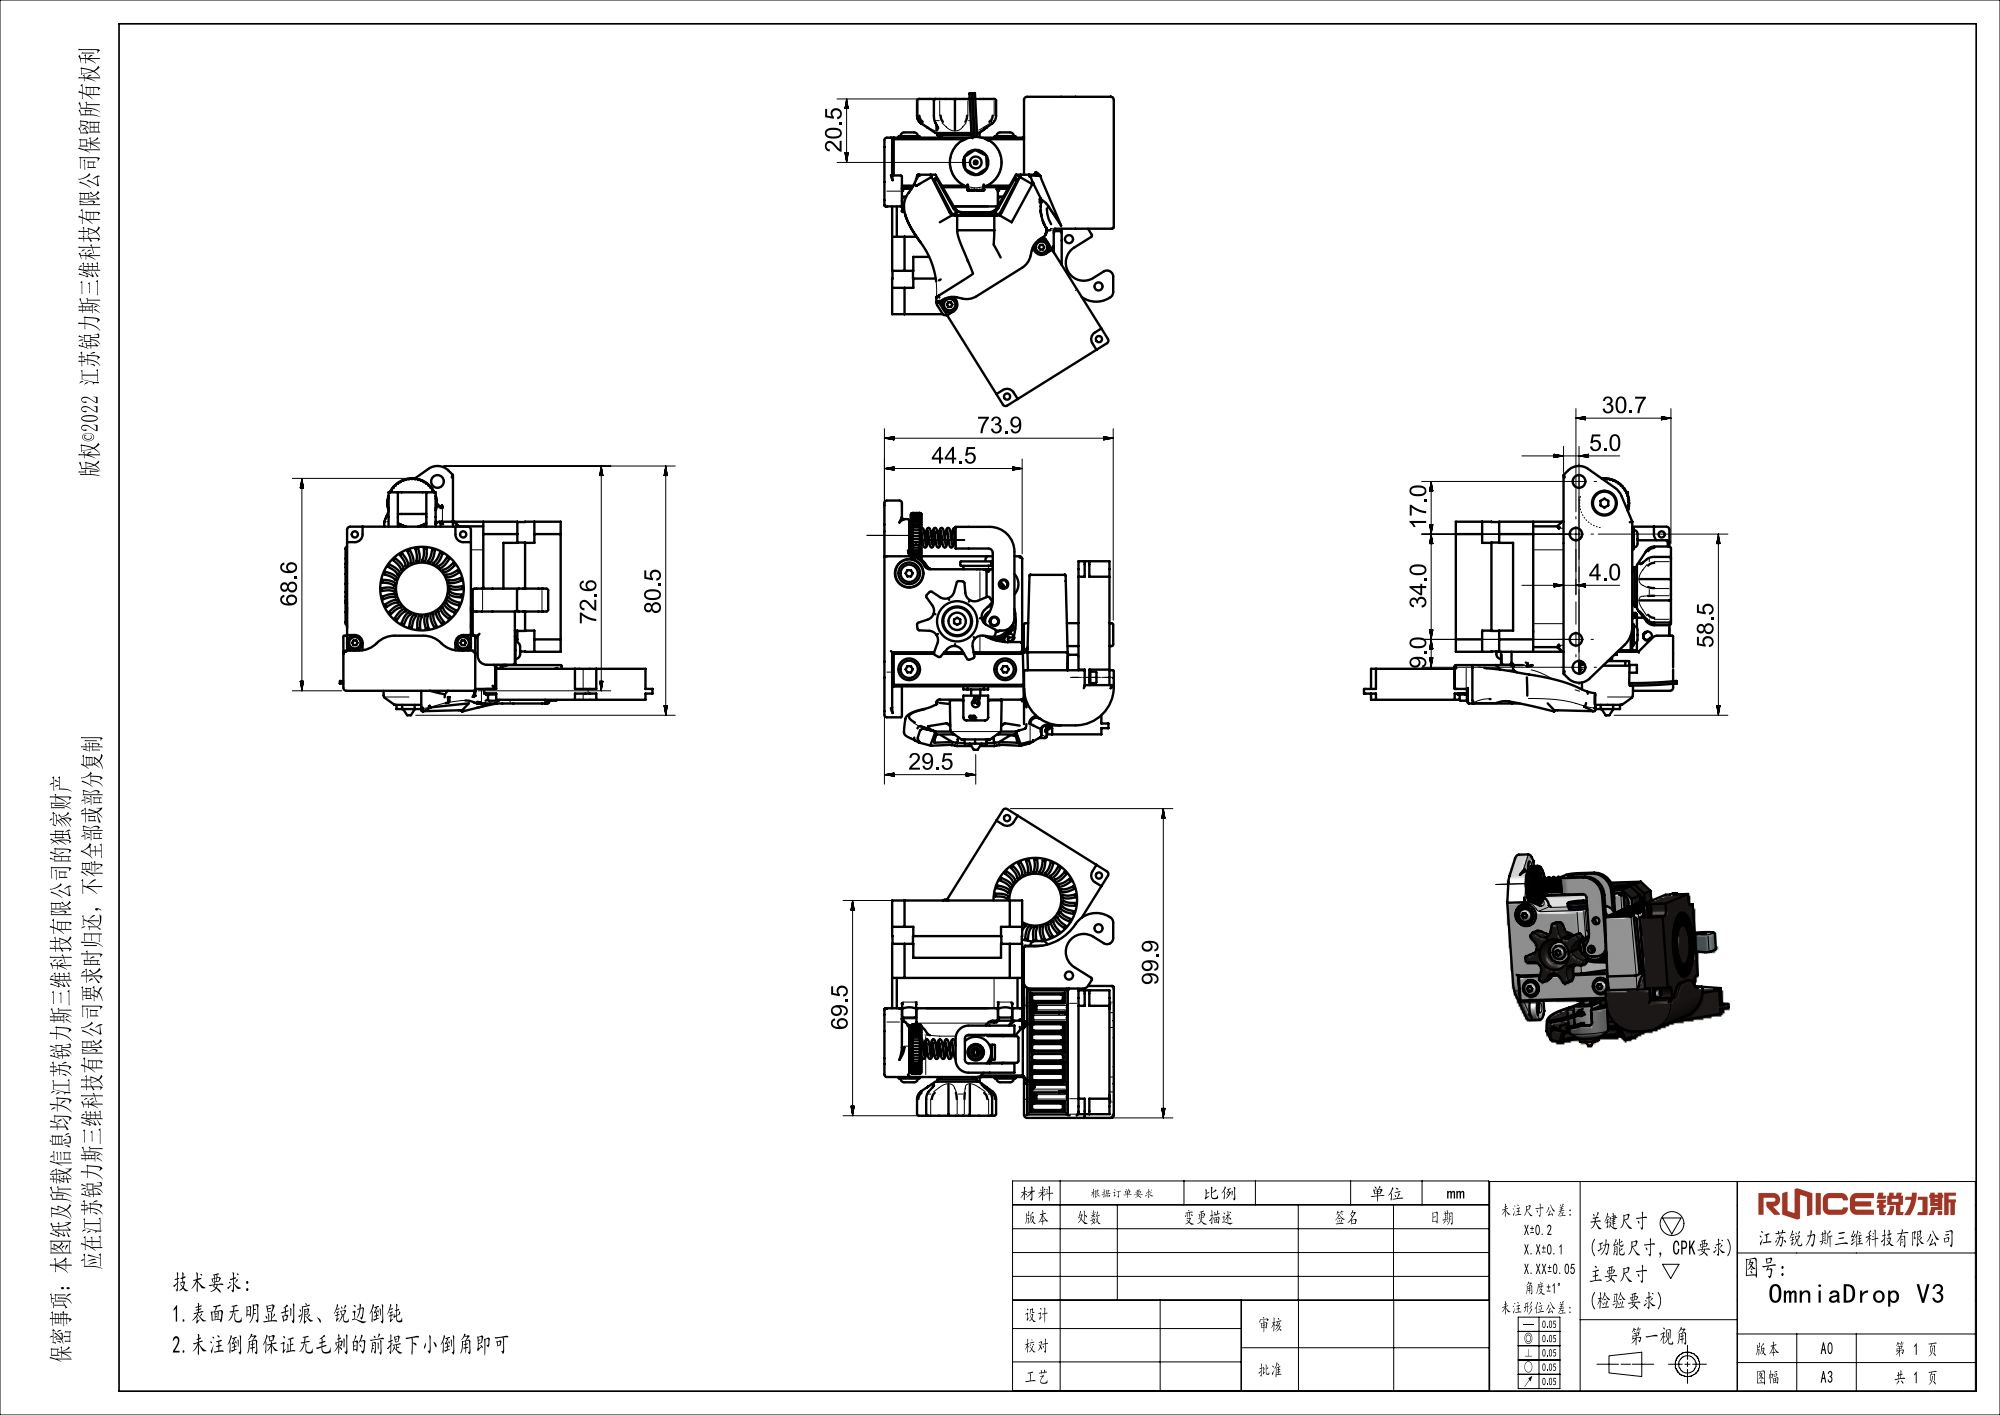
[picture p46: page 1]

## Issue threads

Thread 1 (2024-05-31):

v3 Instruction Sheet is incorrect

Tylersuard, 2024-05-31:
Page 1 mentions a 6mm insert, but does not show it in the diagram.  Instructions do not mention the heat insert needed for the manual knob.

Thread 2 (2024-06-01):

STEP files contain incorrect pieces

Tylersuard, 2024-06-01:
The main body of the extruder in the step file has no way to attach the extruder to a 3d printer.  Now I have to re-print the body and build the whole thing all over again...

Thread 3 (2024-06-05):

The BL Touch mount does not fit a BL touch

Tylersuard, 2024-06-05:
It is the wrong size for the holes, and also for the distance from the build plate.

Tylersuard, 2024-06-05:
My mistake. The mount wraps around the yellow part of a BL Touch.

Closed 2024-06-05.
